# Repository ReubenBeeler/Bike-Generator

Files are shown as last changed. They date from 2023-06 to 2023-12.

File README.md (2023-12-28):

View this README in light-mode for best results.

# Bike-Generator
Authors: Reuben Beeler, Audrey O'Malley, Cora Constantinescu

Thumbnail

### WELCOME!
This repository is a collection of 3D-model files for our UCSB Physics 13CL, 10-week project -- a bike-driven, permanent-magnet generator that can power auxiliary electronic devices (such as a mobile phone). The final product was a stationary bike where the back wheel of a mobile bike was replaced with our mechanical generator, which was securely attached to the gears and frame of the bike. If you are interested in building a similar project for yourself, continue onwards! This is a comprehensive set of instructions for building our project (with special notes along the way to make the journey as seamless as possible!). 

The first detail to note about this project is that there are a few crucial, pre-existing components in this design which we had to work around, namely a permanent magnet, a USB charging cable, and a bike with a $135\\,\text{mm}$ rear frame/hub spacing. The design of our circuitry and 3D-printed parts had to meet the specifications and sizes of each of these components, so naturally this manual is segmented into 3 chapters. (Note that such objects come in a variety of flavors, so it is likely that slight modifications need to be made to fit your exact needs). Before we dive in, here is a brief overview of the required materials.

### Materials and Budget
The cost of the entire project, for those who already own a bike, is around $200. Do note that the below table indexes the costs of each component, even though not all materials will be fully used. For example, PLA filament typically comes in batches of a kilogram, yet the project only demands a couple hundred grams (if all parts are printed successfully).

| Item | Price |
| --- | --- |
| [30 AWG Magnetic Wire](https://www.amazon.com/TEMCo-AWG-Copper-Magnet-Wire/dp/B00IAZYI3M)  | $36.36 |
| [Indoor Bike Stand](https://www.amazon.com/SONGMICS-Indoor-Trainer-Reduces-USBT01B/dp/B07YJLTQRD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)  | $59.99 |
| [Bike Sprocket](https://www.amazon.com/EBIKELING-7-Speed-Bicycle-Freewheel-Cassette/dp/B07C86GR9W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)  | $18.98 |
| 2 608Z Ball Bearings | $10 |
| [Bridge Rectifier](https://www.amazon.com/Bridgold-KBPC5010-Rectifier-Electronic-Silicon/dp/B07MQ65HLB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) | $8.99 |
| [Jumper Wire Kit](https://www.amazon.com/dp/B07CJYSL2T?psc=1&ref=ppx_yo2ov_dt_b_product_details)| $11.99 |
| [5V Voltage Regulator](https://www.amazon.com/dp/B07T5ZHY63?psc=1&ref=ppx_yo2ov_dt_b_product_details)| $13.99 |
| [Heat Sink](https://www.amazon.com/dp/B07ZMH4FDW?psc=1&ref=ppx_yo2ov_dt_b_product_details) | $6.99 |
|[Magnet](https://www.amazon.com/gp/product/B07KF61YZT/ref=ppx_yo_dt_b_search_asin_title?ie=UTF8&psc=1)| $16.99 |
|3D Printer Filament| $20.00 |
|Galvanized Hex Bolt: 3/8 inch diameter, 1 inch long| $2 |
|Galvanized Hex Bolt: 3/8 inch diameter, 2.5 inch long| $2 |
|2 Galvanized Hex Nuts: 3/8 inch diameter| $2 |
|Bicycle| -- |
|Desired USB Powered Electronic Device| -- |

## 1. Generator
At the heart of this project lies the generator itself, which consists of a magnet and a coil that move relative to each other. There are lots of moving parts to consider, so in order to construct a successful generator, one should know the appropriate optimizations and constraints of electromagnetic generation. To this end, it is important to understand the physical laws which govern such phenomena; below is a brief overview.

### The Physics

Permanent magnets have a permanent magnetic field. For a cylindrical magnet polarized along its cylindrical axis (like the one used in our project), a cross section of the magnet and its magnetic field looks like the following:

cylindrical_magnet_field_lines

If you were to spin the magnet along its cylindrical axis, the magnetic field in 3D space would be unchanged since that axis is the axis of symmetry. If, however, you were to spin the magnet on another axis, the direction and magnitude of the field at a particular point would change as a function of time. If, perchance, this changing magnetic field penetrates a conducting material or loop of wire, the conductor will experience an induced emf characterized by Faraday's Law (equation below).

Faraday's law

We see that the induced voltage ($\mathcal{E}$) in the conductor is linear to the change in magnetic flux ($\Phi$) with respect to time. So, a spinning magnet near a coil/solenoid induces a voltage which drives current through a circuit, thus powering some electronic device. Note that for a magnet spinning inside a single solenoid, the induced current is _alternating_ current.

### Optimizations

Before building or buying anything (magnets, magnetic wire, 3D print filament, etc.), realize that there are several considerations and optimizations to be made!

#### Magnet Strength
It is natural to search for the strongest magnet (or rather the most densely strong magnet since space is an important consideration). A permanent magnet's strength is characterized by its "maximum energy product", which specifies the greatest value of volumetric magnetic-energy density on the surface of the magnet. This is a good metric for characterizing magnetic field strength because volumetric magnet-energy density is a monotonic function with respect to magnetic field strength. Specifically, it is the following:

magnetic energy density

Finding the right magnet can be difficult since there are several strains of magnets on the market! To help navigate the sea of shiny metals, consider the following graph of magnet strength over recent decades from a ScienceDirect article by Mohapatra and Liu:

magnet strength graph

It is clear that neodymium-iron-boron magnets win the cake with maximum energy products reaching as high as 58 mega-guass-oersted. (The abbreviation for such a neodymium magnet is naturally N58). Unfortunately, such magnets are challenging to get any hands on; the best _accessible_ magnets for DIY projects have strengths around 50 mega-guass-oersted. [Our specific magnet](https://www.amazon.com/gp/product/B07KF61YZT/ref=ppx_yo_dt_b_search_asin_title?ie=UTF8&psc=1) is a cylindrical N52 magnet, which does its job (although is more expensive then essentially identical magnets from other vendors). If you buy multiple N52 magnets together, the first difficulty will be separating them. Slide them apart, don't pull, and **NEVER** bring them back together unless you know what you are doing. These magnets are hazardous!; bringing them together will likely break them in addition to your fingers. Keep them away from computers, hard drives, and electronic devics in general.

#### Magnet-Coil Orientation
The first optimization we make is maximizing the emf (change in magnetic flux) by orienting the magnet and coil such that the axis of rotation is perpendicular to both the cylindrical magnet's axis _and_ the axis of the solenoid. Here is a visual supplement to thwart confusion:

Cylinder-Magnet Rotation Axis

#### Magnet Shape
While cylindrical or rectangular magnets are common, they are not ideal for a generator. Recognizing that the magnet performs circular motion relative to the surrounding coil, the magnet might as well be symmetric around the axis of rotation. Since this axis is perpendicular to the axis of the coil (a circular solenoid), a spherical magnet would utilize this "rotation space" most efficiently. We accordingly recommend that future versions use spherical N52 magnets as opposed to cylindrical N52 magnets. The rest of the project assumes a cylindrical magnet because that is simply what was available at the beginning of our project.

#### Proximity of Coil
Where in the magnetic field diagram is our cylinder?... Maximizing magnetic flux (and emf, current, etc.) in our generator is achieved by maximizing the enclosed field lines per loop of wire in the coil. For a single loop of wire whose axis of symmetry would appear vertically in the field diagram, it is visually evident that the loop should be placed immediately around the cylinder to enclose the maximum number of field lines. While it is interesting to consider the optimial radius for a loop of wire with some offset along the magnet's axis, the coil will not be sufficiently large to justify further exploration of this topic; the optimal location of the coil given our needs is as close to the magnet as possible.

#### Rotor and Stator
What spins and what doesn't? An electromagnetic generator simply requires a magnet to move relative to a coil (which is wrapped around a hollow cylinder). In the user's reference frame, the magnet could spin or the coil could spin (or both!). To optimize for simplicity (to avoid the difficulty of wire brushes), the coil and cylinder (called the "stator") are kept stationary relative to the bike while the permanent magnet and "magnet holder" (called the "rotor") rotate inside the coil. To help understand what that might look like for our cylindrical magnet, the standalone rotor (magnet and magnet holder) looks like this:

Rotor

The rotor combined with the cylinder looks like this:

Cylinder Right smaller
Cylinder Front Right smaller

#### Angular Frequency
How fast do (should) we spin the magnet? If the magnet is spinning with some constant angular velocity, the magnetic flux would look like

phi equation

where $\Phi_0$ is a constant depending on the geometry of the magnet and coil. Using Faraday's Law, we find that

emf as function of omega

So, increasing angular frequency of the magnet increases the induced emf, which pushes more current across the load. This is what we desire, yet it is important to note that operating at too high frequencies increases friction between the rotating and stationary parts of the build. This implies the existence of an optimal frequency, yet the constraint of a human turning the magnet with only mild gear reduction makes this optimal frequency beyond reach; an oscillatory frequency of about 5-10Hz is sufficient as we'll see later.

#### Number of Wire Windings
Consider a solenoid with a variable number of windings. Increasing the number of windings of the solenoid quadratically increases the absolute value of magnetic flux (and its time derivative), thus increasing the absolute value of the induced emf. In general, more wrapped wire provides more electrical generation. However, realistic wires have some resistance! Having an inductor with an enormous amount of wire (relative to the impedance of the load) would be counterproductive since most of the energy would be dissipated by the inductor's resistance. So, there must be some optimal amount of wire to use in the inductor. Unfortunately, due to the complicated nature of the various dissipative forces, it is difficult to predict what exactly that optimum is.

#### Wire Size
Which size of wire should you pick for the coil?... We use copper wire as it's a good, cheap conductor. Knowing the resistivity of copper wire and the expected impedance of the load (about $5\\,\text{k}\Omega$), we calculated an optimal wire gauge of about 35 AWG. This calculation maximized inductance of the solenoid over resistance of our circuit while keeping constant the volume of space filled by the wire of the solenoid (since magnetic field drops off quickly). This was a crude sort of calculation but was enough to support an argument for a very thin wire... so thin that the 35 AWG wire is difficult to handle without breaking, so we resorted to using a [CMS Magnetics 30 AWG wire](https://www.amazon.com/gp/product/B07XPS2MSM/ref=ppx_yo_dt_b_search_asin_title?ie=UTF8&th=1) for the solenoid.

**Post-project note:** In hindsight, a thicker wire (around 25 AWG) would have been a better choice for allowing more current without overheating the wire: our magnetic wire was rated for $0.2\\,\text{A}$, which was easily exceeded. With the voltage regulation of $5\\,\text{V}$ for USB charging, the output power was limited to the order of a watt. For a more powerful USB charger (our end goal), we advise using a thicker wire.

#### Wire Insulation
Typically, wires are insulated using a flexible variant of PVC. This is great for increasing durability of dangling wires, however it is very space-inefficient for constructing a solenoid. The common solution for such a problem is buying wire with an enamel coating, called _magnetic_ wire. This enamel coating has a darkish-orange color similar to copper and is notoriously difficult to strip. Typical wire strippers are generally incompetent for removing enamel coating (especially on very small wires such as 30 AWG), so the next best methods are a) scraping with a knife or scissors and b) using sandpaper of roughly P200 grit.

#### 3D-Print Filament
This project involves a decent amount of 3D printing, and printing the provided STL files with the wrong settings can easily break a build. Choosing the correct settings comes with experience, but choosing the correct materials can be done from the get-go. The filament used in our final project was PLA, a 3D-printing standard which worked sufficiently well. Some problems introduced themselves when printing the magnet holder, which has threads of diameter $8\\,\text{mm}$ and pitch $1.25$. Printing the rotor horizontally flat, even with layer height of $0.05\\,\text{mm}$$, leads to enough imprecision when printing the threads that a nut cannot be screwed on (a problem which becomes evident later). Printing the rotor vertically fixes the layer-height imprecision issue, but causes the rotor to be weaker under torsion. This allows the rotor to break easily when given a strong rotation acceleration. In the end, the rotor was printed horizontally with increased shell count to solve the torsion issue, while we used a tap set to fix the imprecise threading issue.  During your 3D-printing, ensure that the layer height is $0.05\\,\text{mm}$ when printing the threads. Additionally, the rotor (and any other parts which experience significant stress) should be printed with about 80% infill to prevent breaking.

We did experiment with TPU, as it is a flexible and more durable alternative to PLA, but thread precision and tapping is an issue; it is a notable candidate worth trying, but PLA does the job.

### Building
Given the above information, the design of the generator follows accordingly. The magnet holder slides through a slit in the cylinder, after which the magnet may be inserted. The magnet holder, as depicted above in the Rotor and Stator section, fits around our magnet snugly without the need of an adhesive. In order to stabilize the rotation of the rotor, we use two 608Z ball bearings ($8\\,\text{mm}$ inner radius, $22\\,\text{mm}$ outer radius, $7\\,\text{mm}$ height), one on each side of the rotor. The outside of the bearings are stationary with the cylinder and fit snugly into the two circular slots, while the inside of the bearing rotates with the rotor. The bearings (depicted as gray disks) are visualized below: top view is on left, bottom view is on right.

Bearing and Nut 1
Bearing and Nut 2

In the above pictures, two 3D-printed nuts (in black) keep the rotor in the correct vertical alignment. Without such nuts, the magnet is attracted to one bearing or the other, pulling the rotor far enough to one side that it collides with the inside of the cylinder.

The next obvious step is to create the coil, which should be wrapped as close to the center as possible for reasons discussed earlier. Our generator functioned with just 300 turns; the exact number depends on your needs.

Finally, we should test the generator, which requires a method of rotating the rotor. A simple hand-crank is a practical solution for testing and debugging. The provided hand-crank in this repository is essentially an extension of a nut which screws onto the longer threaded side of the rotor as seen below.

Cylinder Hand Crank Interface

### Testing
In order to test that our generator was working properly, we used both a fan motor and a hand crank to drive the rotor. An oscilloscope trace of the output is below.

ac scope trace

Then, we tested the voltage amplitudes at different frequencies and compiled their results to produce the the following plot.

Voltage vs Frequency

Here we see a linear relationship between frequency and voltage maximum. This is confirmed by theory and gives us the following value of $\Phi_{0}$.



## 2. Circuit
Most devices powered through USB take a voltage input of 5V DC. This motivated our next goal of converting the AC output from the generator into a usable DC current. We used the circuit pictured consisting of a bridge rectifier, a capacitor, and a voltage regulator. We used an oscilloscope to collect all of the following scope traces.

circuit diagram

### Full Bridge Rectification
The first part of our circuit is a bridge rectifier which is a set of four diodes arranged such that during the positive half of the voltage period, the current flows through one pair of diagonal diodes, and through the other pair on the negative half of the period. This resulted in a full bridge rectification where the output was an entirely non-negative voltage. This is exemplified by this transition from an AC voltage on the left ranging from -8V to 8V to an oscillating DC voltage on the right ranging from 0V to 8V. The frequency also nearly doubles after rectification since all of the AC troughs were rectified to become positive peaks. 

full bridge rectification

### Capacitor Smoothing
The next component of our circuit is a smoothing capacitor with a capacitance of 47𝜇F. This capacitor acts as a buffer by charging up as the voltage input increases. Then, as the rectifier voltage falls, the capacitor provides the required voltage to keep the overall voltage output steady. This leaves us with a DC voltage. This is demonstrated in the plots below; on the left, the rectified voltage ranging from 0V to 8V is transformed into a constant 7V DC after the capacitor, shown on the right.

capacitor smoothing

At this step, we had to try many different circuit components and arrangements before we achieved this consistent DC voltage; i.e. different capacitor values, adding resistors, and moving them to different locations and orientations in the circuit. It depended on the voltage and frequency we were inputting into the circuit. The most effective method for us was trial and error, so for more drastically different inputs, there may need to be slight alteration to the circuit. 

### Voltage Regulation
The last component of our circuit was a voltage regulator which will generate a fixed output voltage. We chose a L7805 voltage regulator which caps the voltage at 5V– exactly what a USB powered electronic device expects. The voltage regulator works by dissipating the excess power in heat meaning we need to attach a heat sink to it to prevent it from overheating. In the plots below we can see that the voltage regulator transformed the 7V DC input on the left to a 5V DC output on the right. It also smoothed out any small oscillations or noise that can be seen in the input voltage on the left.

voltage regulation

It is important to also note that every voltage regulator will have a dropout voltage. This is the minimum value of the difference between the input voltage and the output voltage for it to function correctly. A 5V voltage regulator has a dropout voltage of 2V meaning that it needs a minimum input of 7V. If less than 7V is provided, regulation will not occur. However, a voltage that is too high can also cause complications. A 5V voltage regulator has a maximum input of 35V. If the input voltage gets too high, you risk damaging the component. 

### Connection to the Power Bank
The final circuit step was to attach it to the power bank in hopes of actually charging it. We used the USB cord that charged the power bank. Cutting it open exposed two wires, a positive and negative (since it is a no-media cable). We hooked those up directly to the positive and negative outputs of our circuit. We were then able to directly plug the cord into the bank.

The power bank did not charge at first. Connecting it to the circuit altered the total impedance of our circuit since the bank has some intrinsic resistance. It caused our smooth DC output to become less stable and have a lower voltage. As a result, we still had to do some more minor adjustments to the value of our capacitor. After some more guess and check, we landed on the 47𝜇F mentioned above. 

## 3. Bike Interface
Recall the main goal of the project... generating power with a _bike_. Attaching the generator to the bike requires some interface between each end of the generator and the bike frame. The side of the bike with the chain should have a set of gears which connects directly to the rotor, forming the rotating interface. The other side of the frame simply connects to the cylinder, both of which are stationary, hence forming the stationary interface. These two interfaces together complete the bike interface.

### Rotating Interface
The gears (which have built-in ball bearings) should rest on a stationary 2.5-inch long, galvanized hex bolt. This bolt will be fastened to the chain-side of the bike using a galvanized hex nut. However, the bolt doesn't just magically fit into the gears; the design for the gear interface with the bolt consists of two 3D-printed parts (shown below). The left piece fits snugly around the head of the bolt, while the right one fits somewhat loosely on top of the gear. A tight fit for the latter piece is not needed as it will be kept in place from lateral pressure when placed on the bike. It also serves as a spacer between the frame and gears; feel free to adjust its width to match the hub and gear spacing on your particular bike.

bolt smaller
gear smaller

Putting the bolt and gears together, it should look something like this:

gear face smaller
gear and bolt smaller

Once that is done, the gear will need to interface with the rotor. Conveniently, there is a set of 6 regular hole patterns in the gears. We capitalize on this by creating an attachment to the rotor (similar to the hand-crank), which we call "gear fingers". The gear fingers have 6 protrusions "fingers" which snugly fit into the 6 holes of the gears. At the center of the gear fingers lies a threaded hole which screws onto the longer side of the rotor, just next to the 3D-printed nut. The next two images show the gear fingers attached to the rotor. Note the bearing, which is just next to the threaded section of the magnet holder. Note also that the 3D-printed nut (which would be inbetween the gear fingers and the bearing) is not present in this photo. (During the process of debugging, you may find that the nuts are not necessary or that only one nut is needed).

gears rotor 1 smaller
gears rotor 2 smaller

Finally, ensure that the gear fingers fulfill their requirement of fitting snugly into the gears. They should look like this:

gears fingers rotor smaller

The galvanized hex bolt from before is not shown in this photo. When attaching the generator to the bike, the gear fingers will cover the head side of the hex bolt while the tail end will attach to the bike frame.

### Stationary Interface
The stationary interface has no moving parts and is consequently a little more straightforward. The cylinder interfaces with the bike using a hex bolt & nut and a single 3D-printed part. The threaded part of the cylinder screws into this 3D-printed interface, which holds in place the 1-inch galvanized hex bolt in a fashion similar to the previous section. The 3D-printed piece appears below.

stat-face smaller
stat-face bolt smaller

Here is a before-after shot of the cylinder to clarify how the result of the stationary interface should look.

cylinder smaller
cylinder stat-face bolt smaller

### Integration Testing!
The entire generator with the bike attachments is finally complete!

full generator

To put the generator on the bike, simply remove the back wheel of the bike and place the bike frame onto the two protruding hex bolts. Screwing on the hex nuts should ensure a tight fit. To ride the bike, prop up the back in whatever way possible! We used an overqualified [bike stand](https://www.amazon.com/SONGMICS-Indoor-Trainer-Reduces-USBT01B/dp/B07YJLTQRD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) designed for cyclist training.

The rotor should spin smoothly when turning the pedals. If the rotor wobbles, adjust the location of the hex bolts on the frame. Note that when moving the pedals sufficiently fast, the rotor may come in contact with the cylinder (if not setup properly) and melt either the rotor or the cylinder, which is pretty cool but also something to be weary of! 

Now that our generator is attached to the bike, we should be able to pedal the bike to output electricity. Before connecting the circuit, we get the following AC generator output:

AC

In the plot, we can clearly see that the voltage is zero before we start pedaling. Once the pedaling begins, the expected AC voltage output is produced. Next, we can add our circuit to obtain a 5V DC output:

DC

Using a multimeter, we measured the current flowing out of this circuit was $0.45\\,\text{A}$. Using the power relation $P = IV$,  we have a final power of $2.25\\,\text{W}$ supplied to the power bank. Note that by adding/changing wire and making a few small modifications, this generator is capable of sustaining much more power output; for the purpose of charging our power bank, however, it turns out that $2\\,\text{W}$ is sufficient.

Now that we finally have all of the elements connected, we can ride the bike and charge the power bank as expected. The blinking lights on the power bank in the bottom-left hand corner of the below video indicate that our power bank is indeed charging.

https://github.com/ReubenBeeler/Bike-Generator/assets/110072246/ba390a81-985c-445b-9bbe-54cf46ee8960

To achieve this constant charging, we needed to pedal at a constant speed. We had to pedal somewhat quickly (about 100 rpm) but not impossibly fast, as shown in the video.

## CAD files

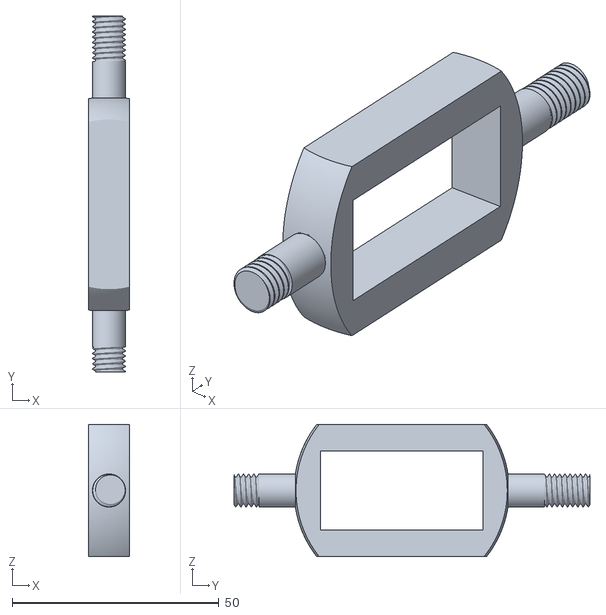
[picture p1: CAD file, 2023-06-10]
stl/Magnet Holder.stl
10.0 x 86.0 x 32.0

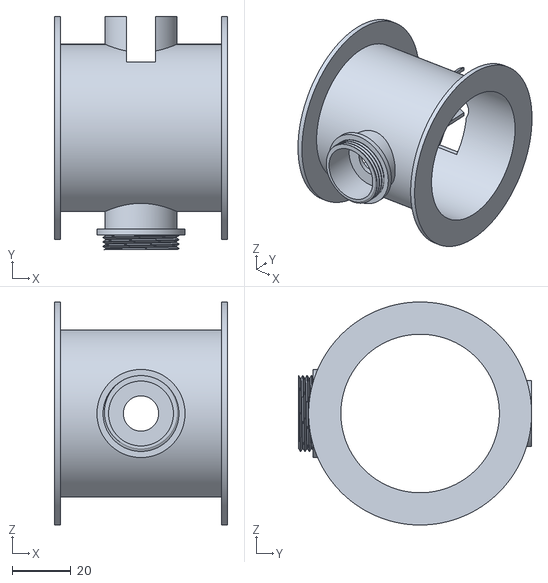
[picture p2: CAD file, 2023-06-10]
stl/Cylinder.stl
59.0 x 79.5 x 76.0

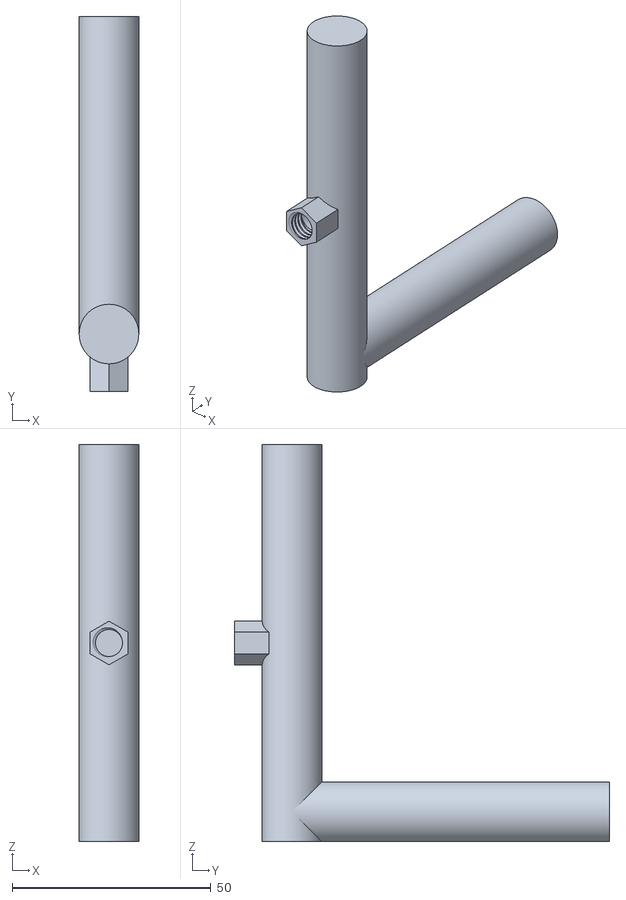
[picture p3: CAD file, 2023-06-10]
stl/Hand Crank.stl
15.0 x 94.5 x 100.0

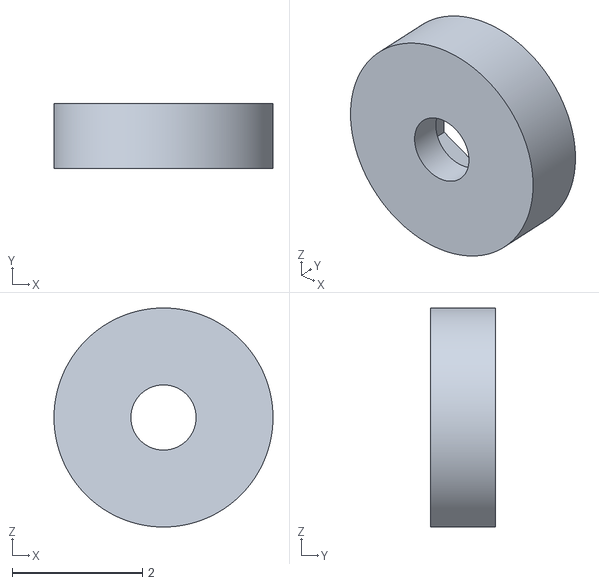
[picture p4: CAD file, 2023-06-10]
stl/Gear-Bolt Interface Head.stl
3.36 x 1.00 x 3.36

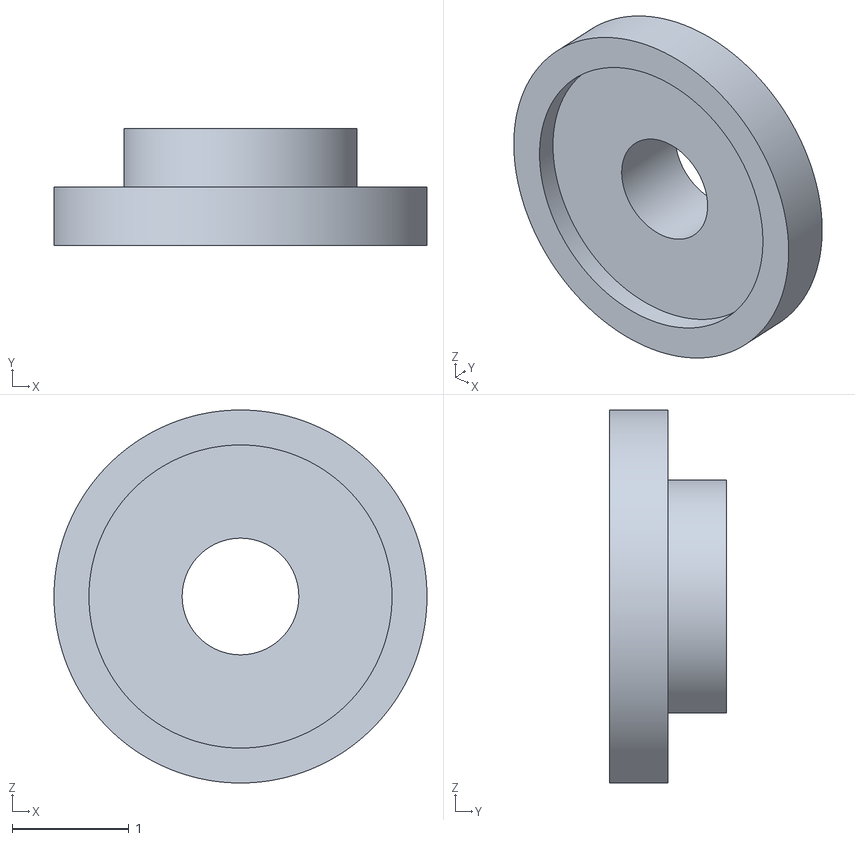
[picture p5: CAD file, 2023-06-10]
stl/Gear-Bolt Interface Tail.stl
3.20 x 1.00 x 3.20

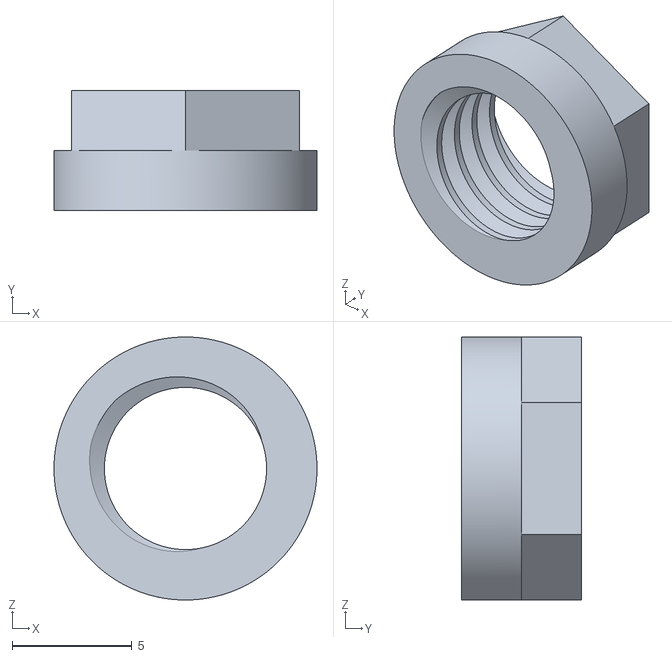
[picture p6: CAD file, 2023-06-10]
stl/Nut.stl
11.0 x 5.00 x 11.0

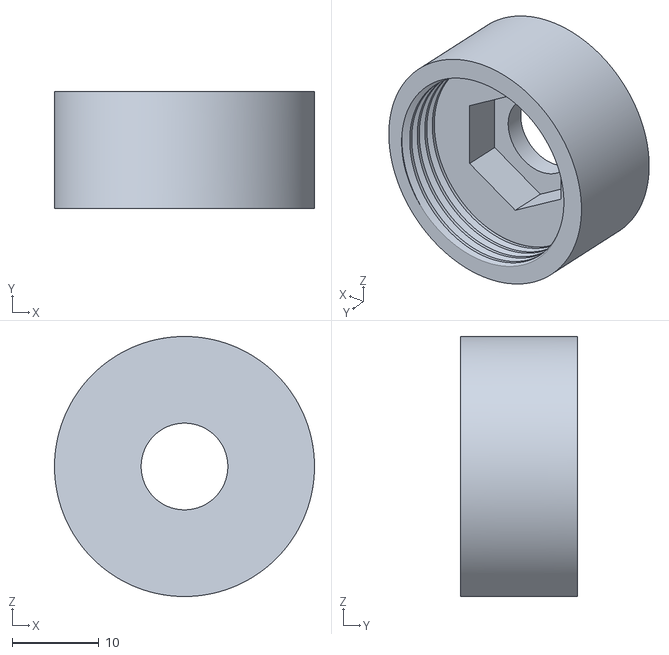
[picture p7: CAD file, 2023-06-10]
stl/Cylinder-Bolt Interface.stl
30.0 x 13.5 x 30.0

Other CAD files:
Gear-Bolt Interface.f3d
Generator Interface.f3d

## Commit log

2023-06-09 readme - magnet strength and shape + some
2023-06-10 STL files
    [Bolt Interface.stl, Cylinder.stl, Hand Crank.stl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]
